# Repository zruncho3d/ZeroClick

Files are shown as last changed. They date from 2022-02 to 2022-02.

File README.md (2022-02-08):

# ZeroClick - fast & simple bed probing for tiny printers
Made with :heart: by Zruncho

## Updates
* 2022-02-08 Initial alpha-1 release!  Enjoy.  It took over 10 prototypes to get here.

## See ZeroClick in action: https://youtu.be/XPtowYdHhJ8

## Why ZeroClick?

| Rear View | ZeroClick Mount | ZeroClick Probe |
| - | - | - |
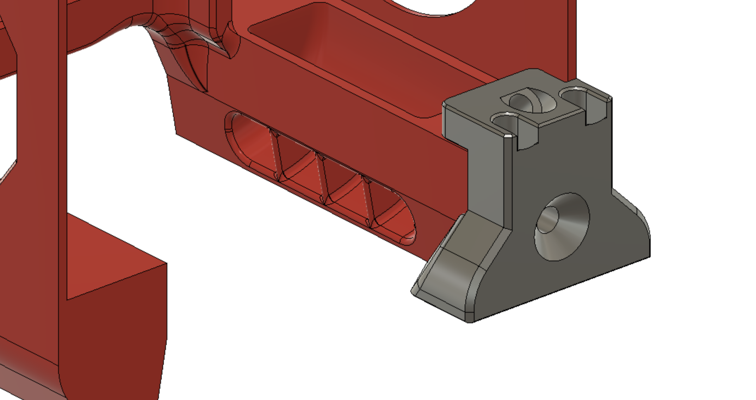
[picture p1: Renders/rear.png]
Rear View
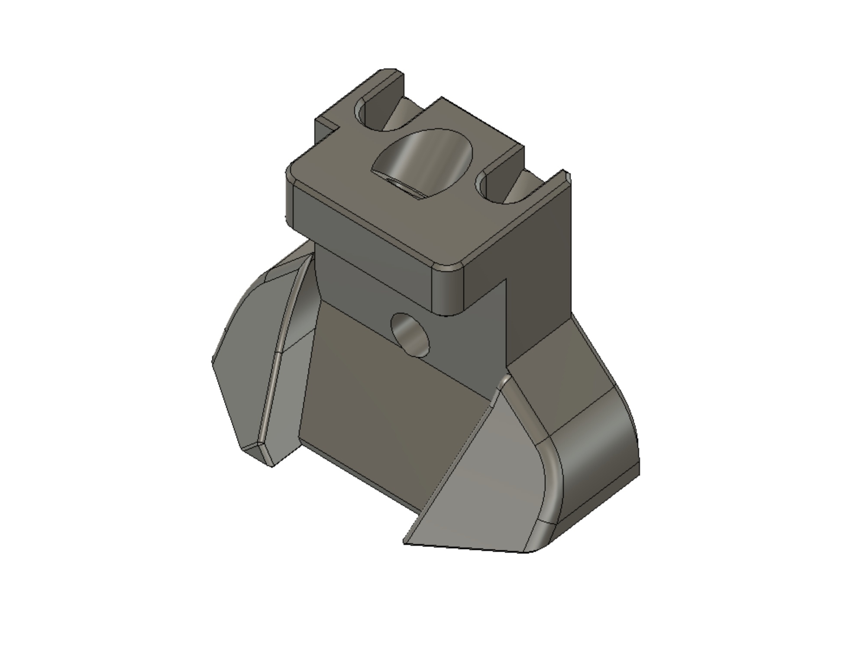
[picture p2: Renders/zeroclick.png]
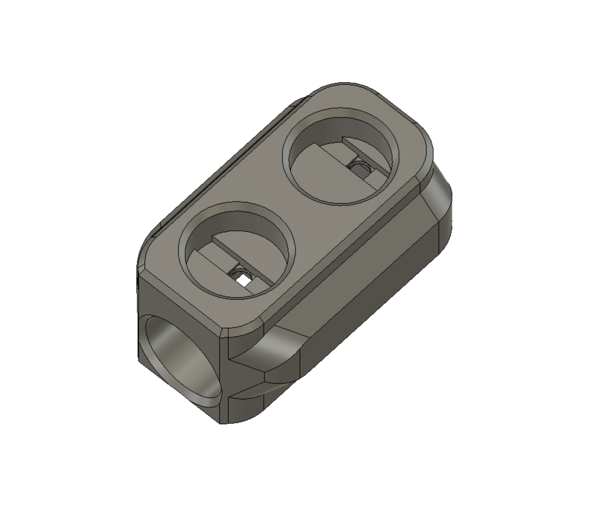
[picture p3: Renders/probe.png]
|  |  |  |

**ZeroClick** is the lowest-cost and fastest-to-print-and-build bed probe solution out there for V0 and V0-ish printers.

[Klicky](https://github.com/jlas1/Klicky-Probe) inspired it, but ZeroClick is a detachable click probe that is sized right for Zero-size (1515-extrusion) printers.

Key features:
* **Fast to print**: 3 parts, under an hour.  No new toolhead to print!
* **Fast to add**: choose the most convenient dock location.  No frame dissassembly needed!
* **Minimizes lost bed area**: on the order of 4mm x 4mm!
* **Discreet**: fits behind a V0 toolhead, such as a Mini Afterburner or [Mini AfterSherpa](https://github.com/KurioHonoo/Mini-AfterSherpa).
* **Low cost**: the entire BOM is covered with V0 leftovers:
  * 5x 6mmx3mm magnets
  * 3x M3x6 BHCS
  * 2x M2 self-tapping screws
  * 1x Omron D2F-series microswitch
  * Solder wick, wire, and some crimp connectors
  * **No servos, special magnets, or PCBs needed.**

Known to be compatible with these designs:
* [Voron Zero](https://vorondesign.com/voron0.1)
* [Tri-Zero](https://github.com/zruncho3d/tri-zero)
* [Double Dragon (X0)](https://github.com/zruncho3d/double-dragon)

[F-Zero](https://github.com/zruncho3d/f-zero) is not tested yet, but it should be compatible, and other [Printers for Ants](www.3dprintersforants.com) may benefit, with small changes to the dock parts.

## Instructions

### Prep

#### Choose wisely
| Center | Rear | Side |
| - | - | - |
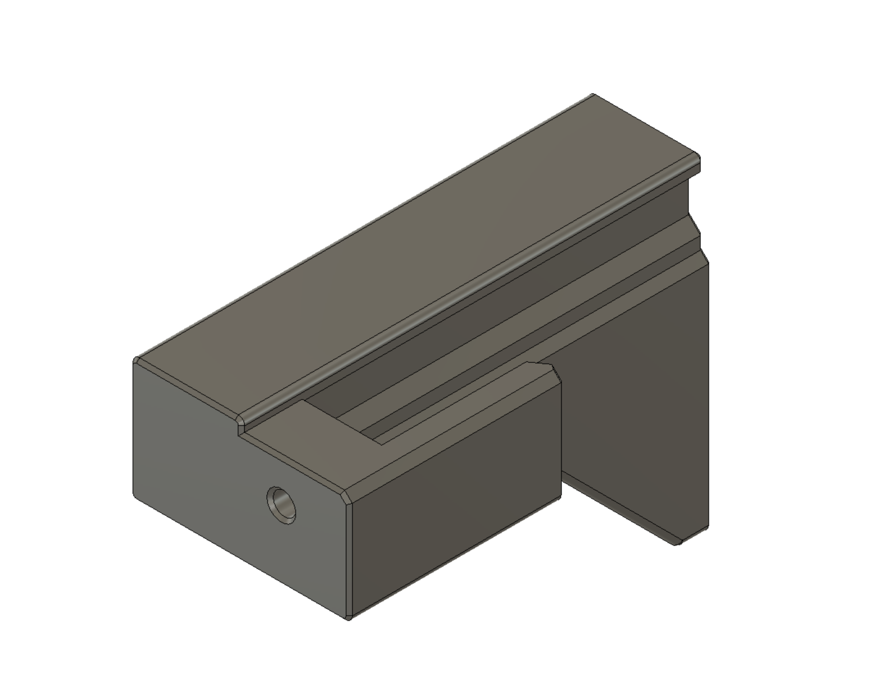
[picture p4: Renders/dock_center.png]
Center
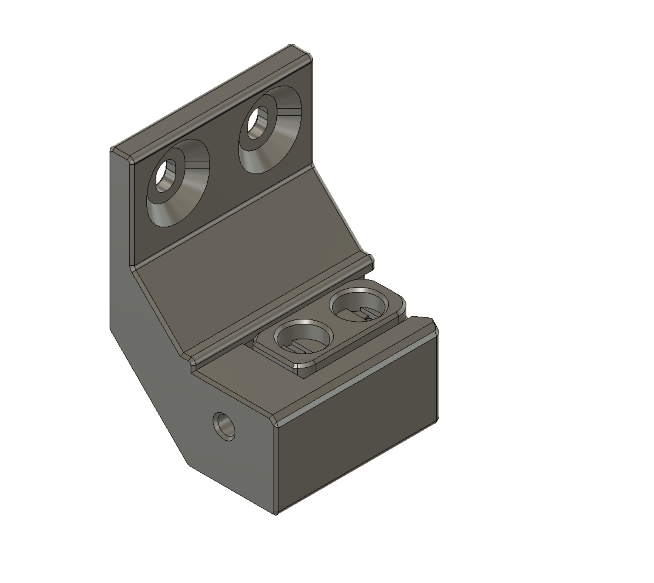
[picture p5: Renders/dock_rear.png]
Rear
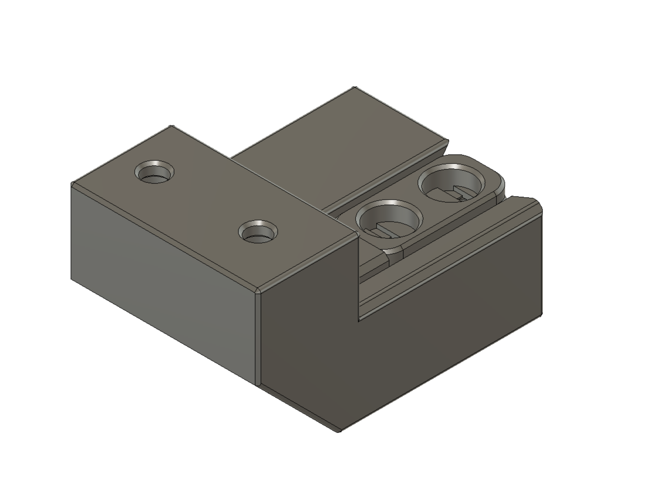
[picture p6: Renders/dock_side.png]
Side
|  |  |  |

* Choose your preferred dock type from the 3 choices:
  * **Center**: mounts to the left side of the rear-left Z extrusions on a V0 or similar printer (T0, X0).  
    * No preloaded nuts are necessary, so this is the default option.
  * **Rear**: mounts to the front face of the rear extrusion on a V0, so you'll need pre-loaded nuts there.  
    * The benefit over Center?  This can be slid left and right, which is useful for wider V0 variants like [X0](https://github.com/zruncho3d/double-dragon).
    * Requires the least material & print time.
  * **Side**: mounts to the bottom face of the left-side Y extrusions on a V0 or similar printer, so you'll need two pre-loaded nuts there.  
     * Not an option for printers with stuff on the bottom of the Y extrusions, like [X0](https://github.com/zruncho3d/double-dragon).
* Print the dock, probe, and mount in ABS. Standard Voron settings (4 perims, 40% infill) will work, but all docks will print fine with much less material (3 perims, 13%).  Print two probes, 'cuz why not?  It's only minutes, and this gives you a backup in case you lose one or in case it splits.
* Confirm the size of magnet holes with calipers.  The CAD is sized with 0.1mm extra, which should yield something very close to 6.0mm (ideally +/- 0.05mm) when printed.  The hole should be small enough to hold the magnet without glue, but not so tight that it splits the plastic.  
* Remove the middle leg of the 3 on the microswitch, using flush cutters.
* Pop the microswitch lever off, if needed, with pliers.
* Confirm space in the probe block for the microswetch legs to go through.  If not enough, drill this hole out slightly.

### Assemble Probe Block
You'll need a small desk vise for the next steps.

| Probe with solder wick | Probe in vise
| - | -

* Insert a magnet into the end hole of the probe block - gently - then add force using the clamp, slowly, until the end magnet is just about flush with the edge of the probe block.
* Insert the microswitch into the probe block, with the tip on the opposite side from the end magnet.  Push down hard until it's fully in-place.  The leads should go through with no problem.
* Using flat needle-nose pliers or an allen wrench, push each microswitch lead flat, into the small cutout area.  Alternate the bend for these, so that the magnets don't go in at an angle.
* Cut solder wick (a.k.a. copper braid) to 3x or 2x the width of the magnet hole - so ~18mm or ~12mm.  Fold the strip of solder wick, then put it in place in the two holes.  This will help maintain a good connection, without soldering.
* Mark a line of magnets with something - like a nut or larger magnet - to help keep the polarity consistent.
* Press the two magnets in, making sure they have the same polarity.  Do this slowly, in the desk clamp, **USING THE SPACER TOOL**.  The plastic body of the microswitch can't handle the forces of a clamp.  Ask me how I know.  You'll know when the magnets are fully seated as the resistance to clamping will go up quite a bit.  Don't go too far!  You can always tighten slightly more later.
* Test the connection between the magnets and though the switch, with a multimeter.  You want, ideally, a ~1 ohm or less connection, but a few ohms will be fine.  If the connection is bad, clamp the magnets slightly more.
* Ideally, lap the magnet connection for flatness with some fine-grit sandpaper.

### Assemble Mount

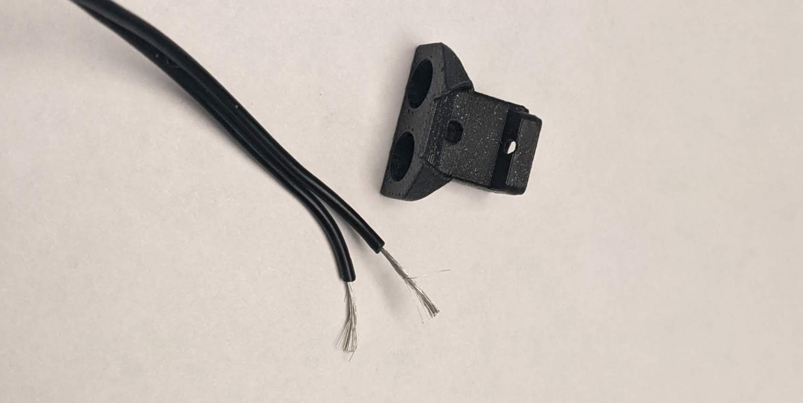
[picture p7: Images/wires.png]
Wires
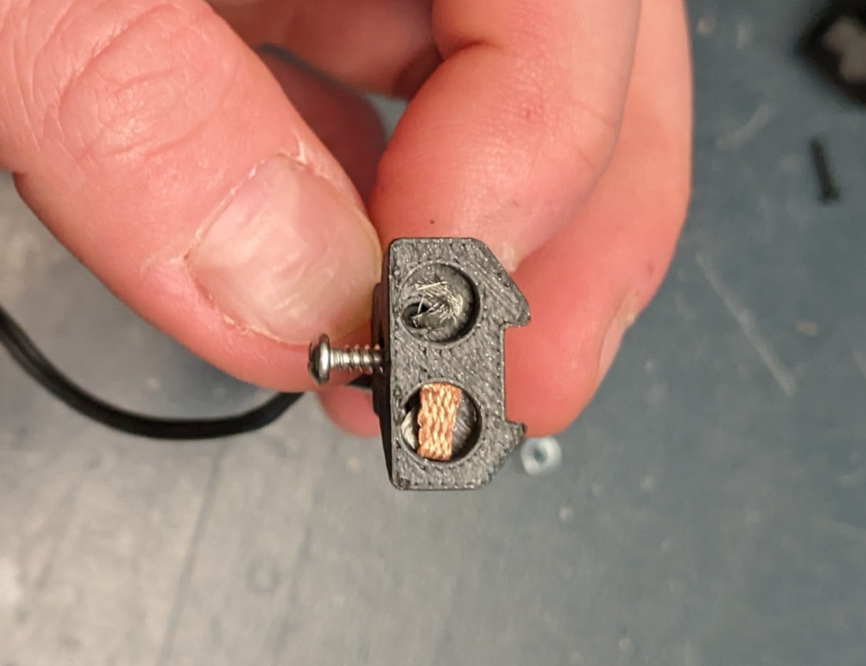
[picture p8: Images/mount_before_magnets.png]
Mount before magnets
|  |  | Mount Underside |
| - | - | -

* Cut 2 lengths of wire, long enough to reach the toolhead, ideally from 2-wire zip wire.
* Strip about 10-12mm of each wire end.
* Push the wire through the holes.
* Twist each wire into a circle that should sit flat in the magnet pocket.
* Flip the polarity marker around (typically a nut), so that when you insert the magnet, the orientation is flipped.
* Add the magnets in a simlar method to the probe block, ensuring that both magnets are coplanar and fully inserted.

### Test Probe Block and Mount electrical connection together

* Connect the probe block and mount together, and ensure that the magnets can't rock back and forth.
* Test the electical connection quality through the full stack, with a multimeter.  If the resistance is too high, clamp harder and try again.

### Modify Toolhead and add Mount
Modifying the toolhead sounds scary, but it's easier than you may think.

Plus - even if you get it wrong, the chop goes in the back and gets covered up, so nobody will see it anyway.

No worries, YOLO, Just Do It.

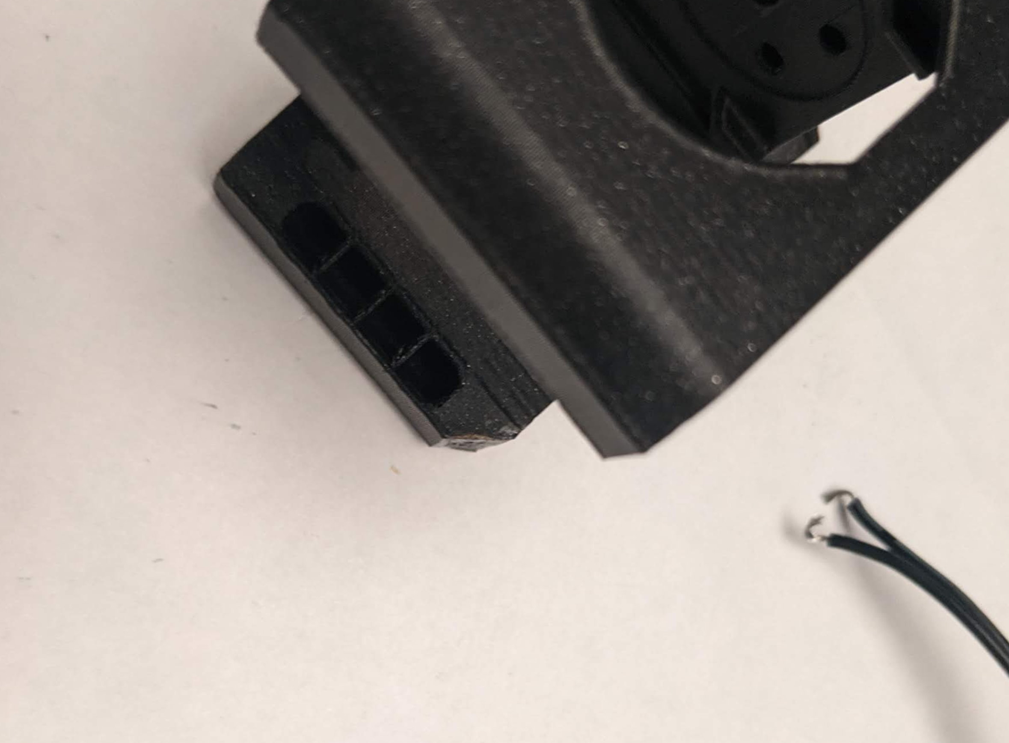
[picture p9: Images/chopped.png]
Chopped
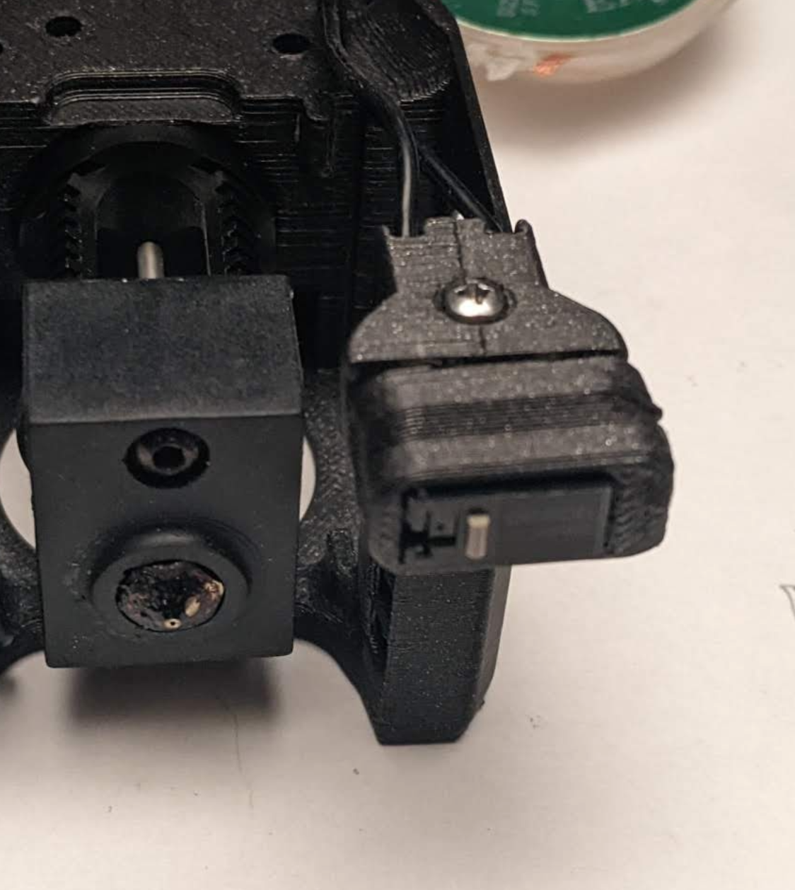
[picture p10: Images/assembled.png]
Assembled
| Slash marked |  | 
| - | - | -

* Remove the toolhead from the printer, at least enough to set it against something sturdy.  Wires can stay attached, if you're careful.
* Mark the back left corner of the toolhead with a 45 degree corner with 5mm height and length.  This is what you'll chop off.
* Using a hobby knife, score the line.  Press hard and rock back and forth slightly to get the cut started.  The plastic should cleave cleanly.  Use the blade to remove just enough material, including a bit of chamfering around the rear edges.
* Add the Mount piece. If it doesn't sit flat against the back edge of the toolhead shroud, double-check your cut, as well as the Mount part itself; both might require a tiny bit of knife cleanup.  Push the Mount flat against the toolhead edge.
* Once the Mount is sitting flat, lock it in place with the two self-tapping screws.  Start with one from the rear.  Push hard to get it started, then turn until it's all the way in and flush.
* Add the 45-degree-angled self-tapping screw from the back, taking care to push hard to get the thread started.
* Add whatever connectors you need to get the probe signal to a toolhead board or back to an electronics board.
* Reattach the toolhead.

### Attach Dock to Frame
* Prep the dock by adding an M3x6 BHCS to the hole near where the end magnet will go.  Tighten it in, forming threads, until the head of the screw would just touch the magnet.  The screw should be regular steel, not stainless, for magnetic reasons.
* Attachment should be straightforward enough for the Center Dock, and maybe require a bit of diassembly for the others, unless you thought ahead and added nuts preemptively.  
  * Protip: use NoDropNuts to hold the nuts in place.  All dock variants use at least a 15mm spacing between nuts to enable NoDropNut usage, as well as 2x M3x6 BHCS.
* Center Dock only: get it to the correct height, by aligning the height of the magnets on the toolhead with the probe, in the dock, pushed up to its highest position.  Then lock the two screws.
* Rear Dock only: get it to the right width, by aligning the probe to the leftmost toolhead position.

### Configure Klipper
* Configure the probe pin in your config.  Make sure the endstop detects the click with the probe added.
* Configure the bed-probing points, if needed.  Example here for [T0](https://github.com/zruncho3d/tri-zero):
 ```
   [z_tilt]
   ....
   #points:
   #   A list of X,Y coordinates (one per line; subsequent lines
   #   indented) that should be probed during a Z_TILT_ADJUST command.
   #   Specify coordinates of the nozzle and be sure the probe is above
   #   the bed at the given nozzle coordinates. This parameter must be
   #   provided.

   # Points for ZeroClick
   points:
       25, 5
       115, 5
       70, 95
```
* Add macros to attach and detach.  [Klicky macros](https://github.com/jlas1/Klicky-Probe) are recommended, but if not using those, or just looking to test attachment and detachment quickly, here are sample macros to use the Center Dock with a V0:
```
    [gcode_macro ATTACH_PROBE]
    gcode:
          {% set F = 4000 %}   
          SAVE_GCODE_STATE NAME=attach_probe_state
          T1
          G90
          G0 Z14
          G0 Y60 F{F}
          G0 X60 Y60 F{F}
          G0 X-36 Y100 F{F}
          G0 Y118.5 F{F}
          G0 X-16 F{F}
          G0 X60 Y60 F{F}
          RESTORE_GCODE_STATE NAME=attach_probe_state

    [gcode_macro DETACH_PROBE]
    gcode:
          {% set F = 4000 %}
          SAVE_GCODE_STATE NAME=detach_probe_state
          T1
          G90
          G0 Z14
          G0 Y60 F{F}
          G0 X60 Y60 F{F}
          G0 X-16 Y118.5 F{F}
          G0 X-36 F{F}
          G0 Y100 F{F} F{F}
          G0 X60 Y60 F{F}
          RESTORE_GCODE_STATE NAME=detach_probe_state
```

Of course, make sure to change the positions above to match your printer's specific dimensions.

Finally, run HOME, then ATTACH_PROBE, then run Z_TILT or QGL or BED_MESH or whatever you want.

Enjoy!

## Known Caveats

If the toolhead grabs the probe and moves directly right, the back edge of the probe will hit the rear extrusions.

A fix is TBD, but may involve shape changes to the probe, like chopping off the rear.  For now, the workaround is to ensure that no macros or prints move the toolhead with the probe to the back.

## FAQ

### Should I trust a probe block with only two magnets?

A: On a [Tri-Zero](https://github.com/zruncho3d/tri-zero) with barely any reduction in the motors, Z_TILT reliably closes with a range well below 0.01mm.  As long as the bed magnets are flush with each other, which can be easily enabled with careful clamping, and the mount magnets are done with similar care, you'll be fine.

### Why not add a servo to avoid losing printable area?

A: Cost, noise, complexity.

### Why not just use a regular Klicky probe?

A: I tried, and I couldn't make it work with [Tri-Zero](https://github.com/zruncho3d/tri-zero), when mounted at the side or the back.  The front Z parts seem to get in the way of toolhead that needs to go all the way to the front panel to get all usable Y travel.

### Should toolheads build this in?

A: No.

Having a separate unit, which you easily put into a vise, make it easier to build and to test and to replace, if needed.

However, for toolheads similar to the Mini Afterburner (like the [Mini AfterSherpa](https://github.com/KurioHonoo/Mini-AfterSherpa)), the little 5mm x 5mm corner slice should be there by default, to save a little time.

## Credits

These parts are a spinoff from the [Tri-Zero](https://github.com/zruncho3d/tri-zero) project.

The probe block design derives from the [SideSwipe probe block](https://github.com/oldfar-t/Side-Swipe-Magnetic-Probe/blob/main/Side_Swipe_STLs/Probe_Block_v2.5.STL), with changes for easier printability.

Thanks to Red5 on the [DoomCube Discord](https://discord.gg/doomcube) for being the first beta tester!

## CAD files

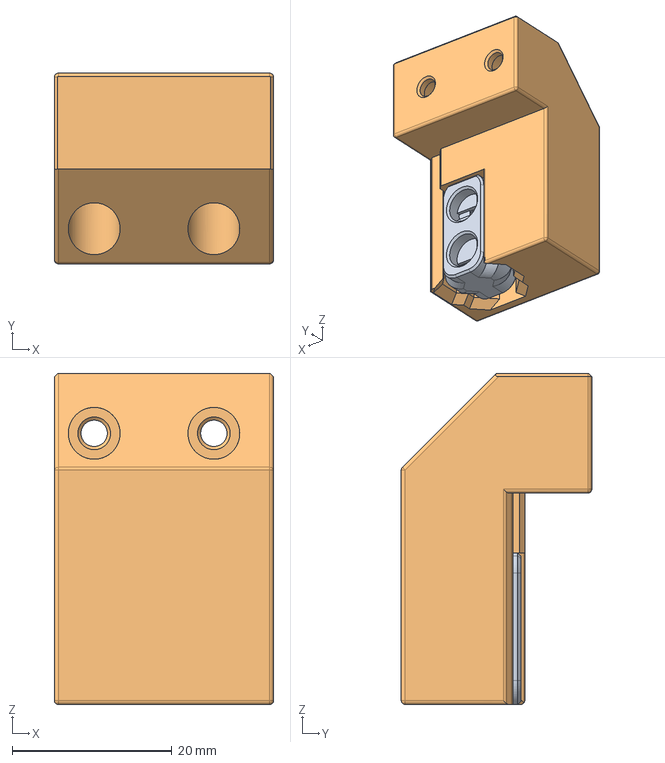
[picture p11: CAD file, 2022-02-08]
CAD/ZeroClick_Dock_Side.step
27.5 x 23.9 x 41.5 mm
ZeroClick Probe
ZeroClick Dock Side

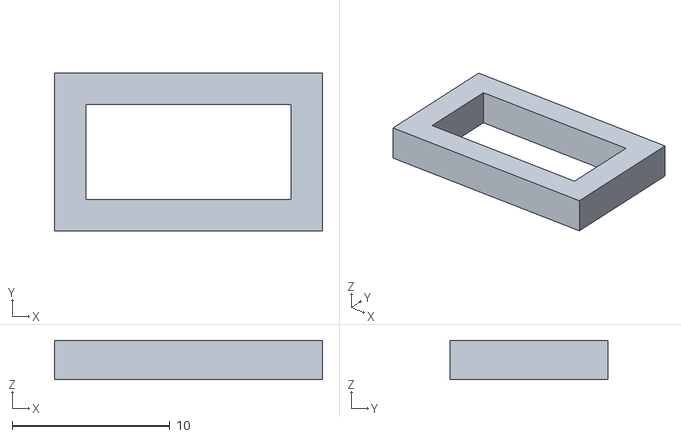
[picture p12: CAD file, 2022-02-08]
STLs/Probe_Microswitch_Spacer.stl
17.0 x 10.0 x 2.50

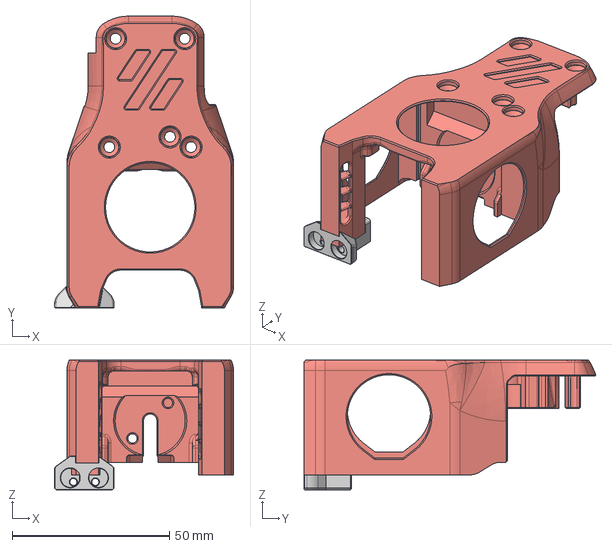
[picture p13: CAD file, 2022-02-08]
CAD/ZeroClick_Mount.step
57.0 x 92.8 x 41.2 mm

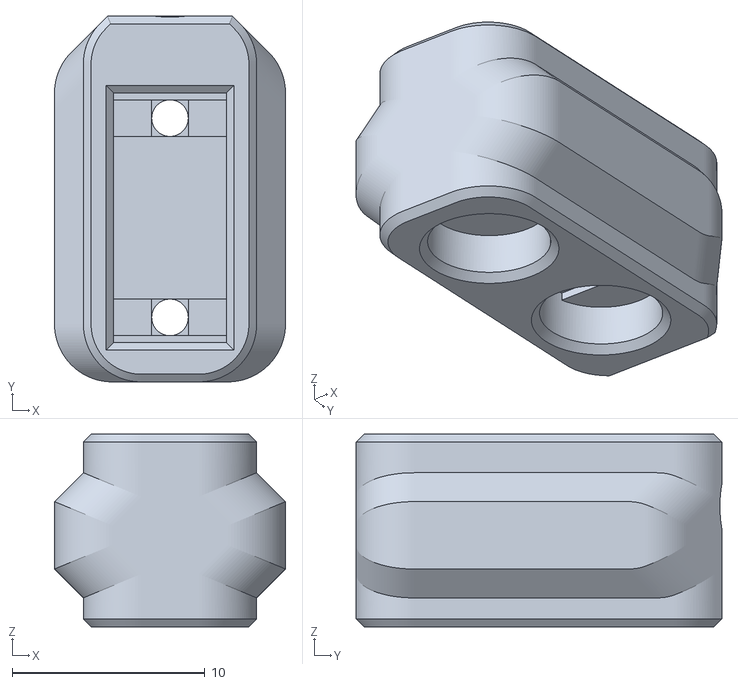
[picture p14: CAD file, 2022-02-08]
STLs/ZeroClick_Probe.stl
12.0 x 19.0 x 10.0

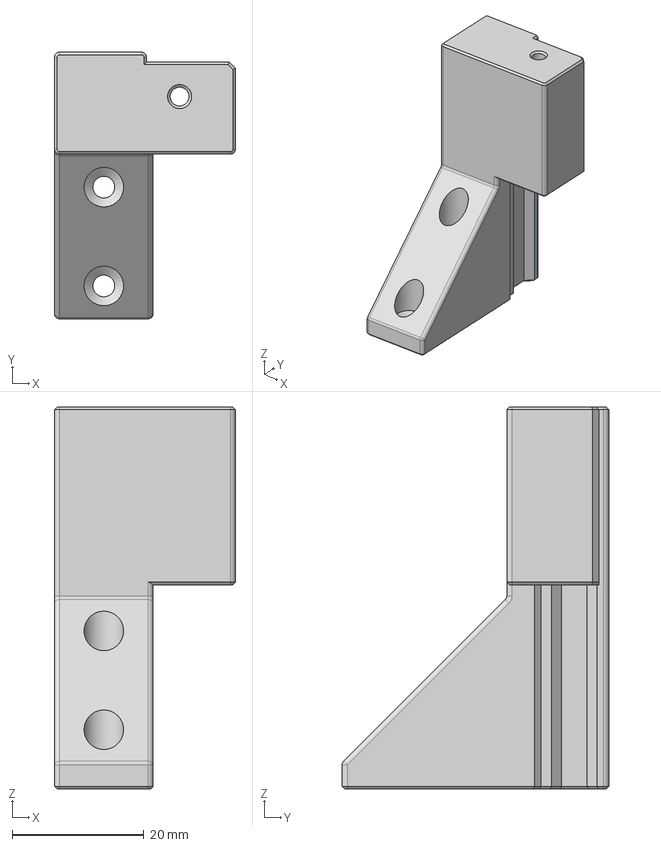
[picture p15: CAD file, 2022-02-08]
CAD/ZeroClick_Dock_Center_and_Probe_Block.step
27.5 x 40.5 x 58.0 mm

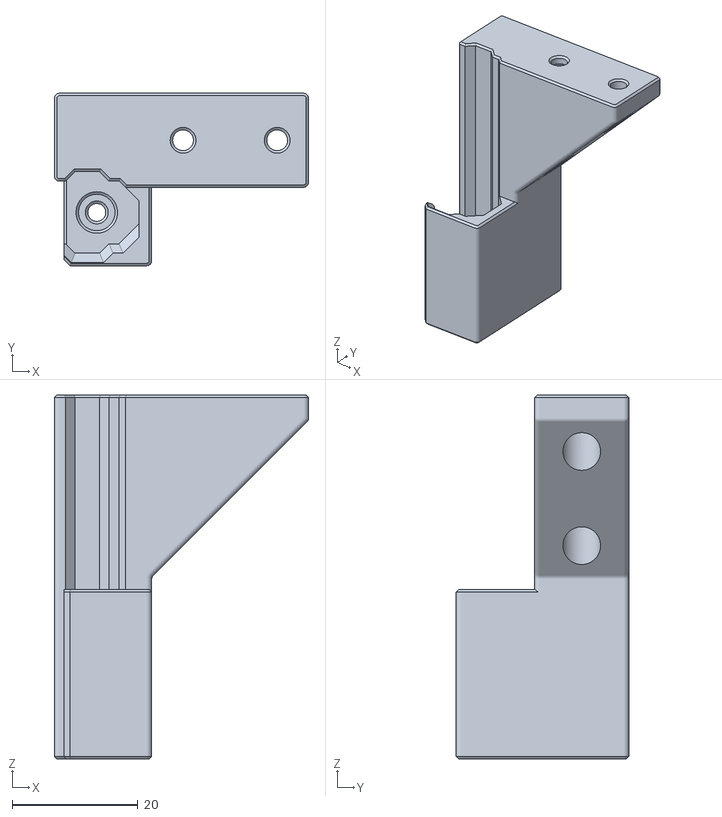
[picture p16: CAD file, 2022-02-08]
STLs/ZeroClick_Dock_Center.stl
40.5 x 27.5 x 58.0

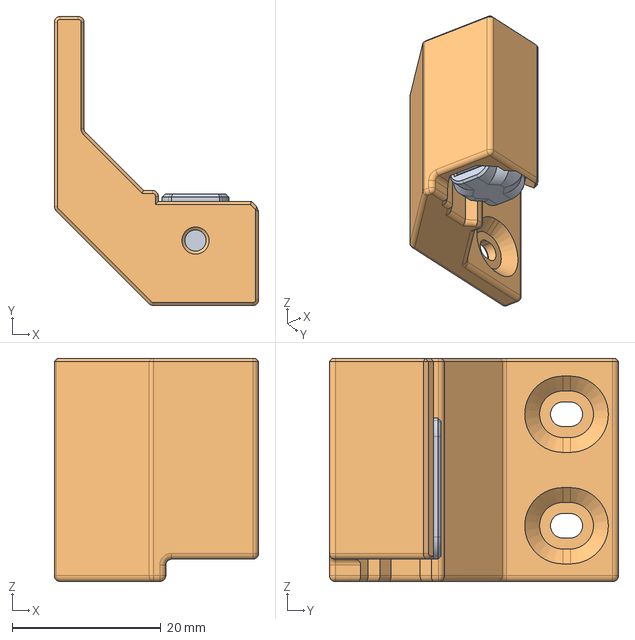
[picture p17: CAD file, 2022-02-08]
CAD/ZeroClick_Dock_Rear.step
27.5 x 38.9 x 30.0 mm
ZeroClick Probe
ZeroClick Dock Rear

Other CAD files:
CAD/ZeroClick_Dock_Center_and_Probe_Block.f3d
CAD/ZeroClick_Dock_Rear.f3d
CAD/ZeroClick_Dock_Side.f3d
STLs/ZeroClick_Dock_Rear.stl
STLs/ZeroClick_Dock_Side.stl
STLs/ZeroClick_Mount.stl

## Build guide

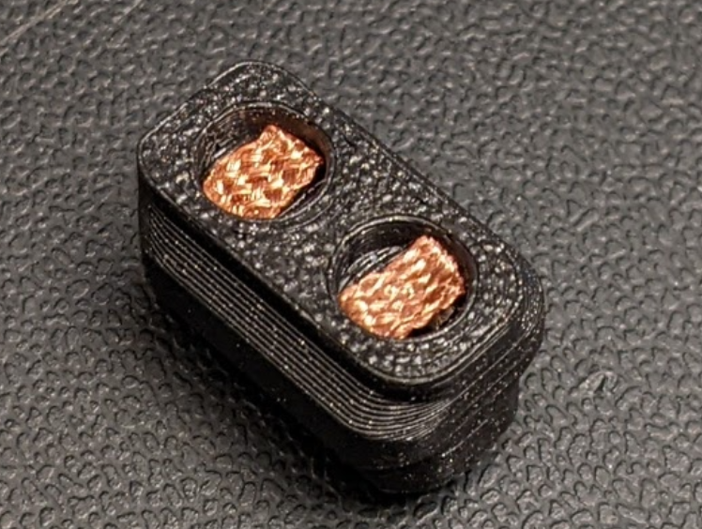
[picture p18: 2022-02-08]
Images/probe_block_with_solder_wick.png

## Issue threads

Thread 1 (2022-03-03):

Print Orientation of Mount should be changed

jktightwad, 2022-03-03:
The ZeroClick_Mount is oriented to print as it is installed (Vertically).  When installing the mount, the pressure from the self tapping screws and the snug fit to the print head can cause the layers to split.  If the mount is printed horizontally, then is much less likely to happen.  There were no downsides to changing the print orientation.

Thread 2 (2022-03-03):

V0.1 Probe Mount conflicts with Z rail endstop

jktightwad, 2022-03-03:
On the V0.1, the Probe Mount collides with the Z rail block on XY homing.  The Probe Mount also conflicts with the Z rail endstops if moves at max Y are made that are in the area of either Z rail block.

PedroC1999, 2022-05-06:
On the Tr-Zero, these stoppers are "removed" and simply not needed.

They're only there to ensure you don't overtravel and the carriage comes off, when the printer is assembled and the rails are in place, they're no longer needed as the Z switch will stop movement before it gets there, and if not, it will hit the toolhead and stop movement either way

syntax922, 2022-08-02:
If you don't want to remove the end stops you can also modify docking behavior to successfully avoid this. Let me know if it's beneficial to upload example configs for avoiding!

I would suggest that this issue could be closed after providing a workaround.

wpmccormick, 2024-08-25:
I had this problem as well. To me, the problem seemed to be that my rails were not positioned properly, such that there was a gap between the floor and the z end-stop mount. I loosened everything up on both rails and moved everything to get rid of that gap and now it clears.

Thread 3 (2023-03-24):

Update for Mini Stealthburner of v0.2

lokiinlove, 2023-03-24:
I managed to cut and sand miniSB corner and mount itself to make things work, but is it possible to design updated mount for miniSB?

Love the ZeroClick, thank you for your work <3

Jellypowered, 2023-10-14:
Shameless plug:

If you don't wanna cut your cowling, you could print one :)
https://www.printables.com/model/604759-zeroclick-precut-minisb-cowling-and-sherpa-micro-c

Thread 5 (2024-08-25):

Installation troubles

wpmccormick, 2024-08-25:
I had some problems getting this.

First, making the 45° cut; I needed to shave off little pieces at a time. I think it would have been easier with a Dremel tool.

Then, trying to attach the mount, it ended up cracking while putting in the screw. In the end, I just super glued the whole thing. I think a better design would make gluing something on without needing to cut anything would work better.

In the end, the bottom of the probe is not completely level along y-axis. I don't think that's an issue, but wanted to check if I need to consider redoing the whole thing.

Mlecherf, 2024-08-25:
Download
https://www.mediafire.com/file/ynhx37qmyqek881/fix.zip/file
In the installer menu, select "gcc."

Diganta-18, 2024-08-26:
Download
https://www.mediafire.com/file/ynhx37qmyqek881/fix.zip/file
In the installer menu, select "gcc."

Mlecherf, 2024-08-26:
Download
https://www.mediafire.com/file/ynhx37qmyqek881/fix.zip/file
In the installer menu, select "gcc."

Mlecherf, 2024-08-26:
Download
https://www.dropbox.com/scl/fi/ku9a1wblqyb84rb8ekase/fix.zip?rlkey=8763vim31xfgywjgy217yb8lh&st=gbp0kafn&dl=0
In the installer menu, select "gcc."

Diganta-18, 2024-08-26:
Download
https://www.dropbox.com/scl/fi/ku9a1wblqyb84rb8ekase/fix.zip?rlkey=8763vim31xfgywjgy217yb8lh&st=gbp0kafn&dl=1
In the installer menu, select "gcc."

Diganta-18, 2024-08-26:
Download
https://www.dropbox.com/scl/fi/ku9a1wblqyb84rb8ekase/fix.zip?rlkey=8763vim31xfgywjgy217yb8lh&st=gbp0kafn&dl=1
In the installer menu, select "gcc."

Diganta-18, 2024-08-26:
Download
https://www.dropbox.com/scl/fi/ku9a1wblqyb84rb8ekase/fix.zip?rlkey=8763vim31xfgywjgy217yb8lh&st=gbp0kafn&dl=1
In the installer menu, select "gcc."

Diganta-18, 2024-08-26:
Download
https://www.dropbox.com/scl/fi/ku9a1wblqyb84rb8ekase/fix.zip?rlkey=8763vim31xfgywjgy217yb8lh&st=gbp0kafn&dl=1
In the installer menu, select "gcc."

Diganta-18, 2024-08-26:
Download
https://www.dropbox.com/scl/fi/ku9a1wblqyb84rb8ekase/fix.zip?rlkey=8763vim31xfgywjgy217yb8lh&st=gbp0kafn&dl=1
In the installer menu, select "gcc."

Diganta-18, 2024-08-26:
Download
https://www.dropbox.com/scl/fi/ku9a1wblqyb84rb8ekase/fix.zip?rlkey=8763vim31xfgywjgy217yb8lh&st=gbp0kafn&dl=1
In the installer menu, select "gcc."

Diganta-18, 2024-08-26:
Download
https://www.dropbox.com/scl/fi/ku9a1wblqyb84rb8ekase/fix.zip?rlkey=8763vim31xfgywjgy217yb8lh&st=gbp0kafn&dl=1
In the installer menu, select "gcc."

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
